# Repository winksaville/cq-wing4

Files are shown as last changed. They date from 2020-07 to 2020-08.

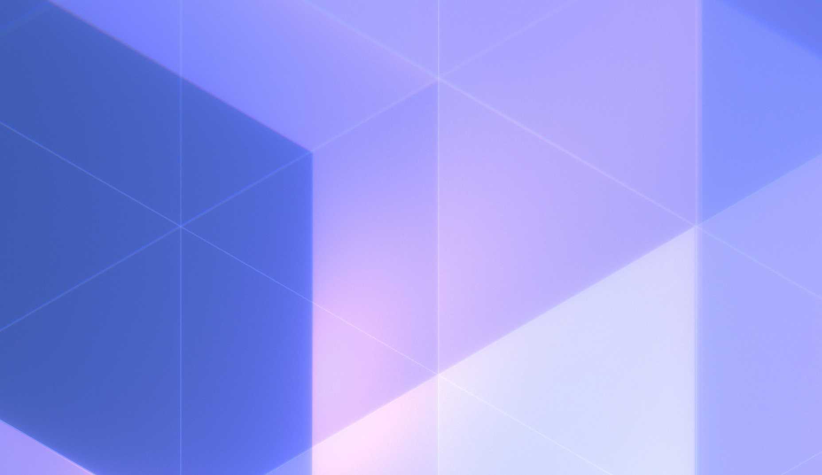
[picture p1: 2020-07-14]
halfWingShell-nrmlTe-shell_+0.1.png

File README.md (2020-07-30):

# Wing with ribs

Wing 4.02

Wing 4.01 had a 8degree kink in the TE so for 4.02 I
flipped the wing over and printed it with LE down instead
of TE down as 4.01 was.

Bad news 4.01 got a kink towards the LE, so that didn't work
and I'll have to change something else, maybe increase diameter
of the cabin.

Another change was to print the dowels with 100% infil up from
50% in 4.01. Because in 4.01 the dowel broke at the wing tail
juncture.

4.02 files pretty well, but took quite a bit LESS ballast on the
nose then I thought it should. I calculated that it should be
about 3.75g but only 1.43g was needed at -60mm.
```
(cq-dev) wink@3900x:~/prgs/CadQuery/projects/wing4 (4.02)
$ ./wing4.02-cg-ballast.py 
noseWeight=7.86g
tailWeight=5.44g
oacWeight=13.3g
oaWeight=13.49g
ballastOffset=-60mm from LE wing
ballast=3.78g
cgLoc=15.00mm from LE wing
cgPct=0.3%
```
It only took 1.43g of ballast
```
(cq-dev) wink@3900x:~/prgs/CadQuery/projects/wing4 (4.02)
$ ./wing4.02-cg.py 
noseWeight=8.15g
tailWeight=6.77g
oacWeight=14.92g
oaWeight=14.91g
ballastOffset=-60 from LE wing
ballast=1.43g
cgLoc=27.12mm from LE wing
cgPct=54.24
```
WHY?

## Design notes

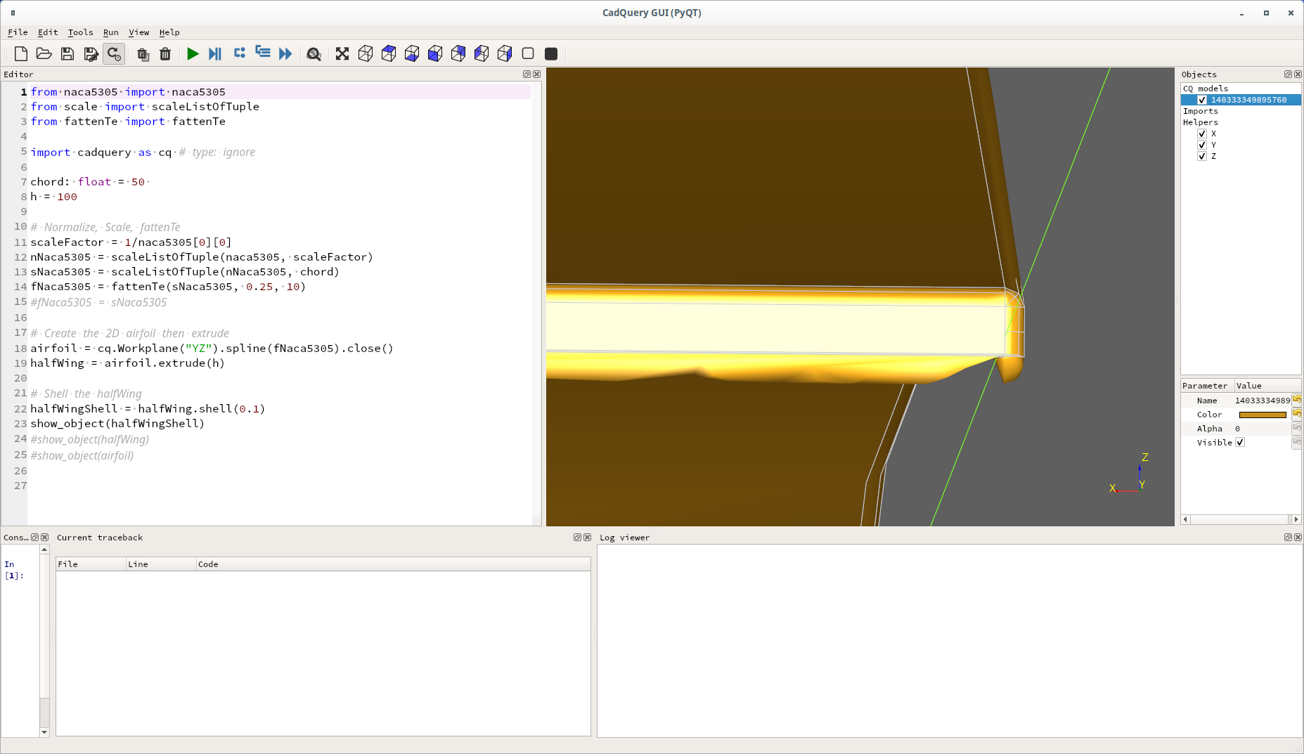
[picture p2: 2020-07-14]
halfWingShell-fatTe-shell_+0.1-yAxis-3.png

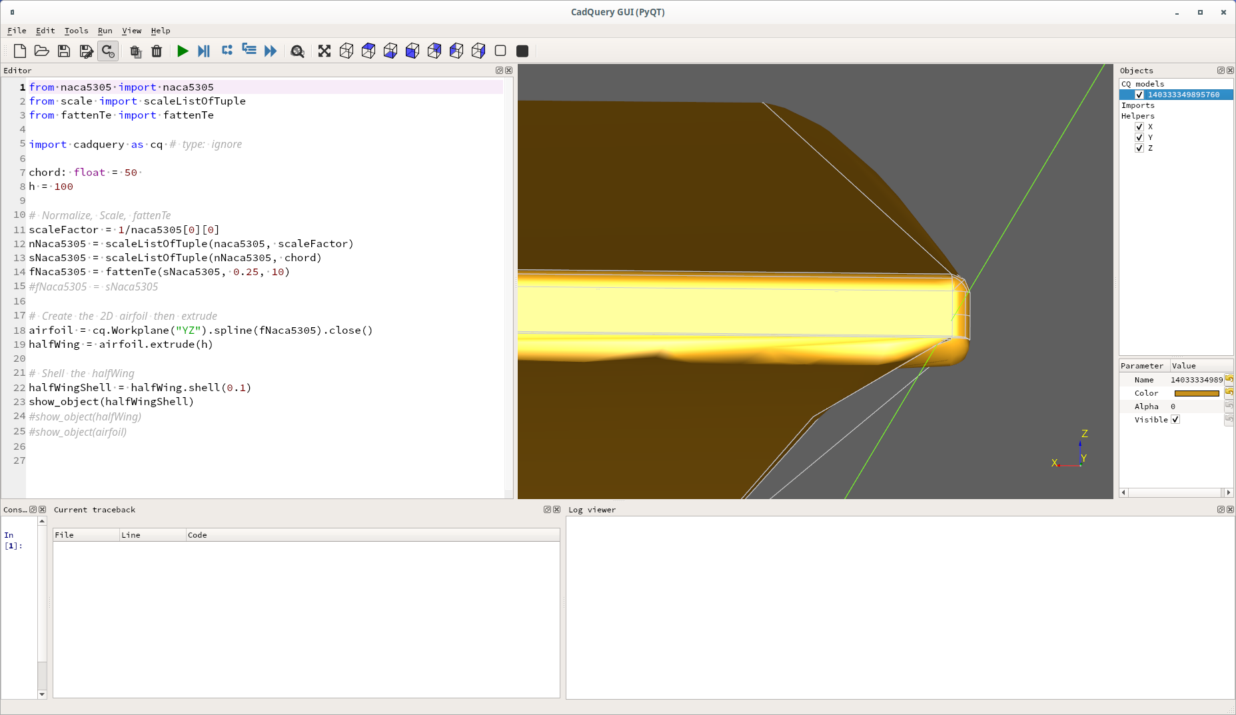
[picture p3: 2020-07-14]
halfWingShell-fatTe-shell_+0.1-yAxis-2.png

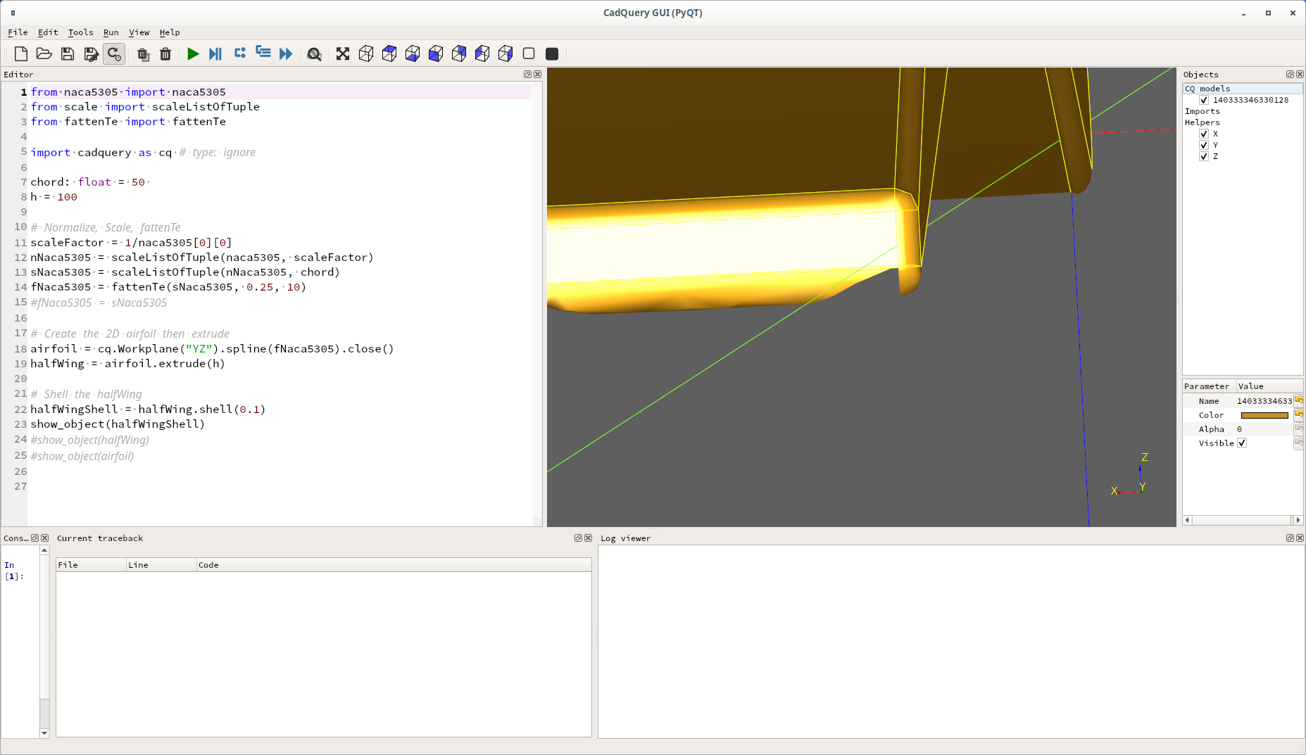
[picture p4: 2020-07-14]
halfWingShell-fatTe-shell_+0.1-yAxis.png

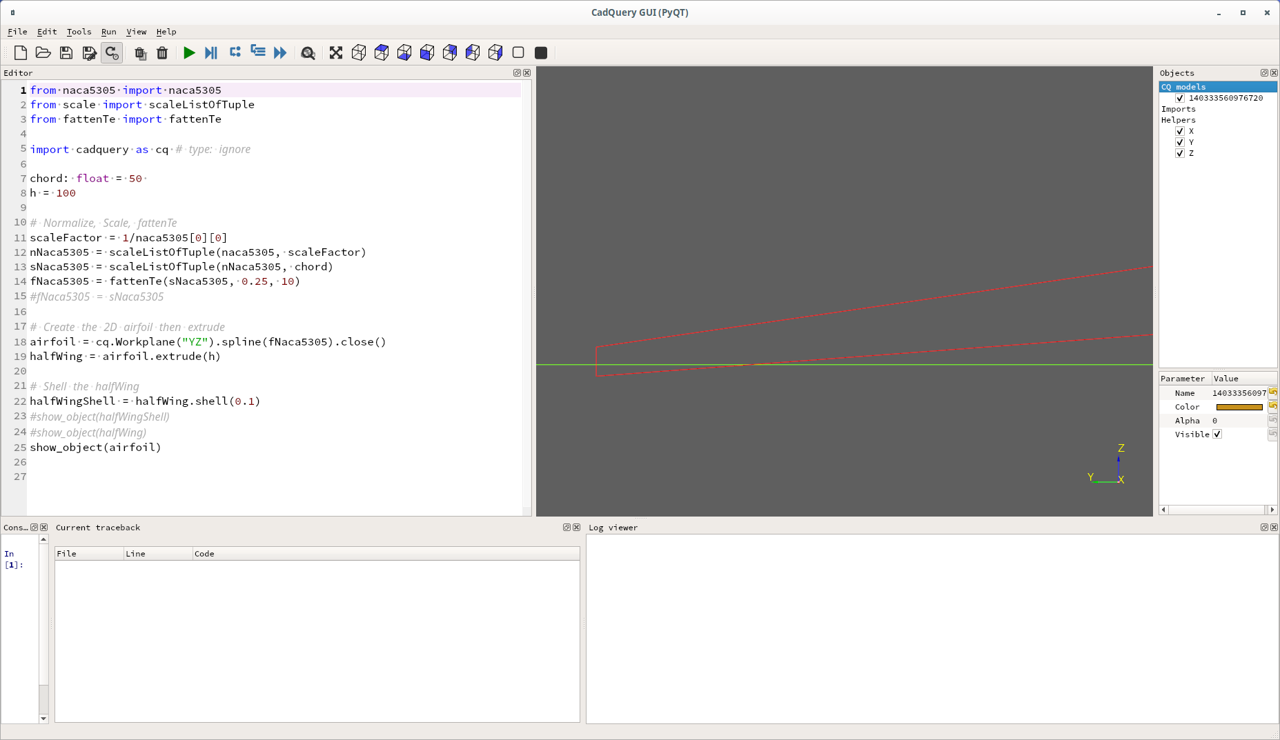
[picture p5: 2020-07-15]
airfoil-fatTe-shell_+0.1.png

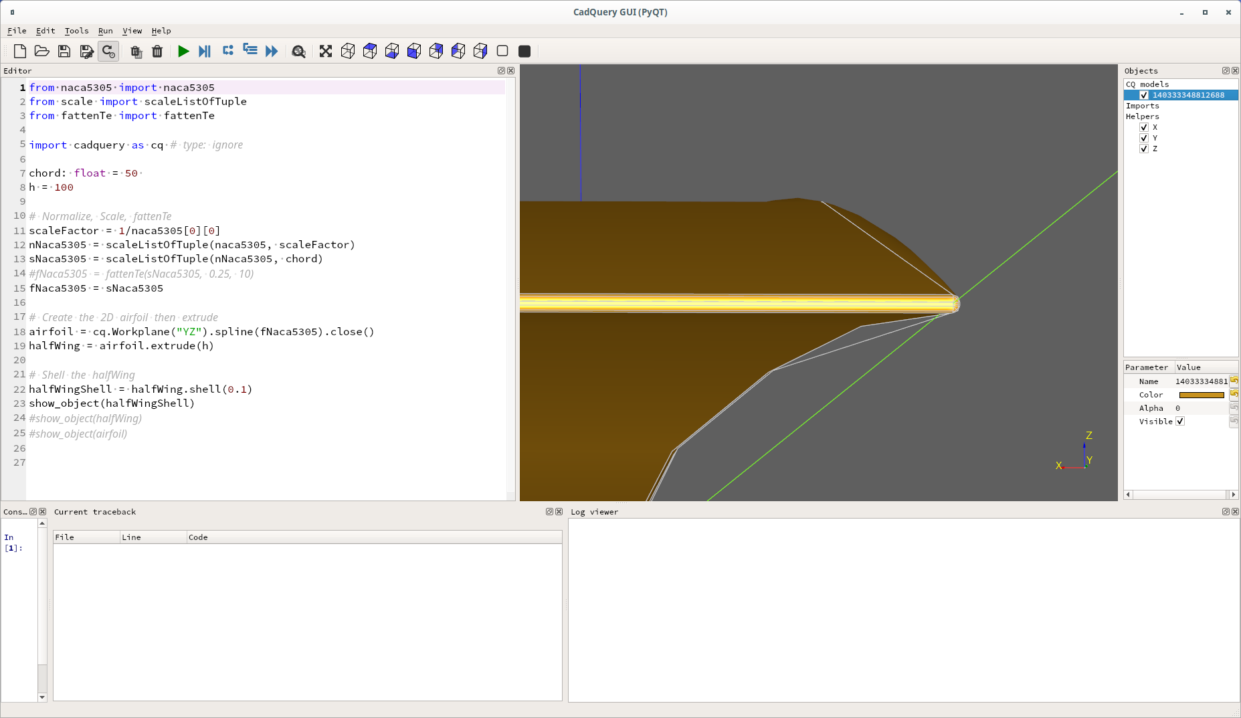
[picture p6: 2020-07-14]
halfWingShell-nrmlTe-shell_+0.1-yAxis-2.png

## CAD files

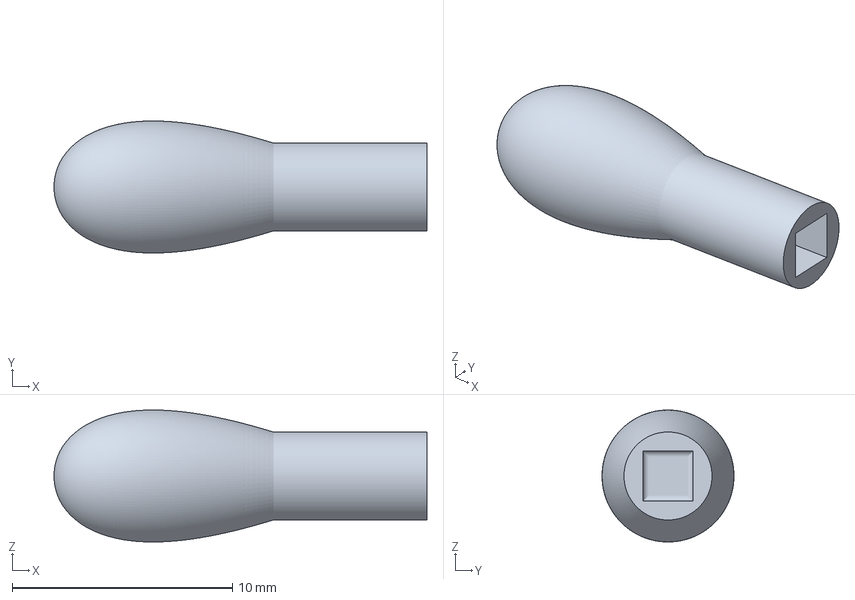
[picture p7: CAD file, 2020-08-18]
ballast-length_22-tol_0.001.3mf
17.0 x 6.00 x 6.00 mm

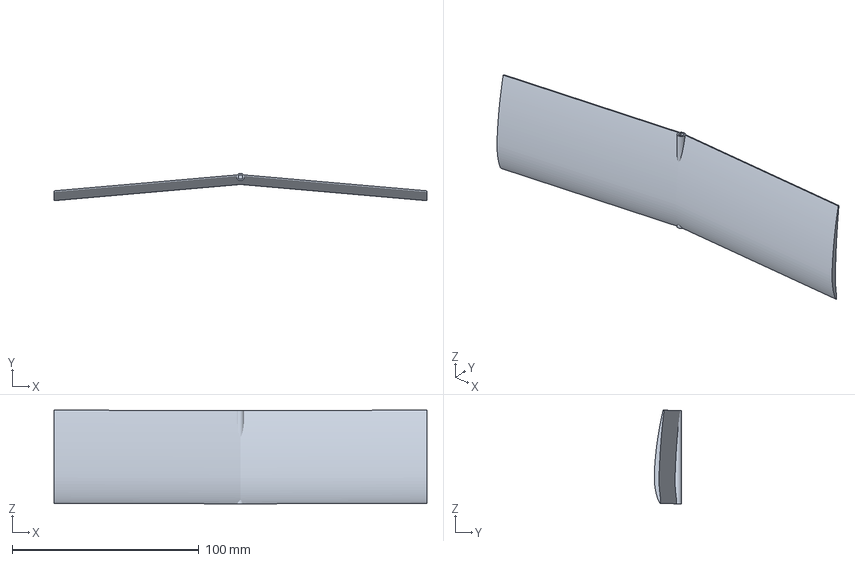
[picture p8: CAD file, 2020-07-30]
wing4.02-LE-down-tol_0.001-ch_50-span_200-di_5-tk_0.26.3mf
200.0 x 14.7 x 50.3 mm

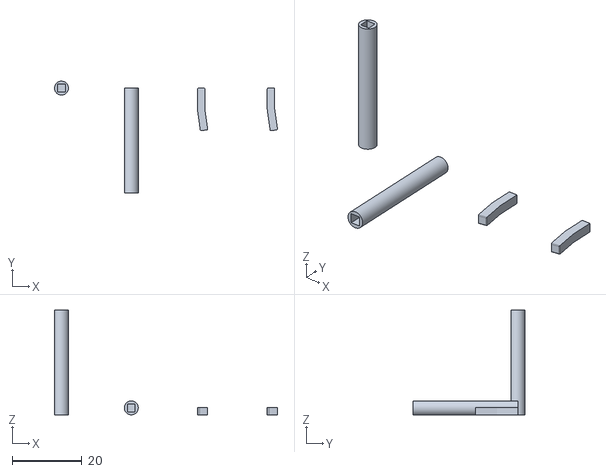
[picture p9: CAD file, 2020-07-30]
rectcon-tol_0.0010-dia_4.0000-x_2.1375-y_2.9402-a_8.0000.stl
63.9 x 32.0 x 30.0

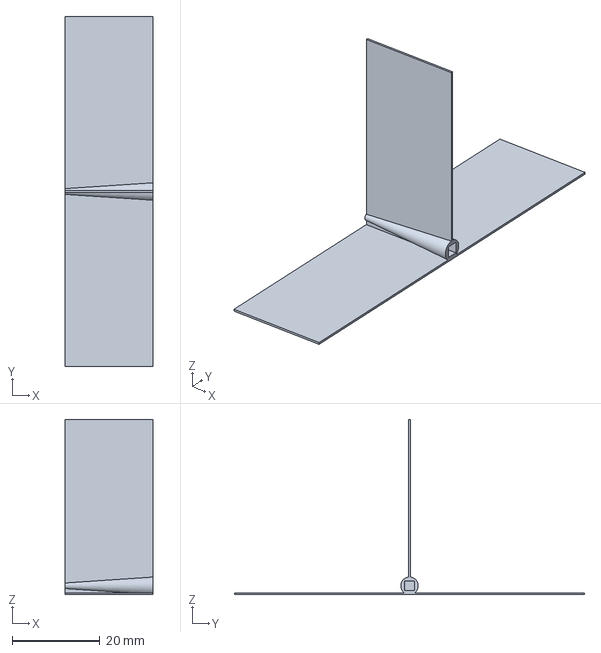
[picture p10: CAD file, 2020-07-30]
tail4-tol_0.001-ch_20-span_80-tk_0.4.3mf
20.0 x 80.0 x 40.0 mm

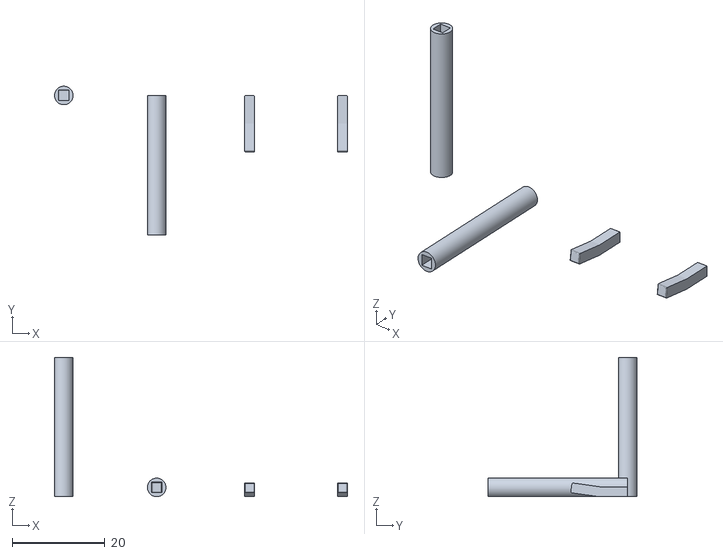
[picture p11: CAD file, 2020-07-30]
rectcon-tol_0.0010-dia_4.0000-x_2.1375-y_2.9402-a_8.0.stl
63.1 x 32.0 x 30.0

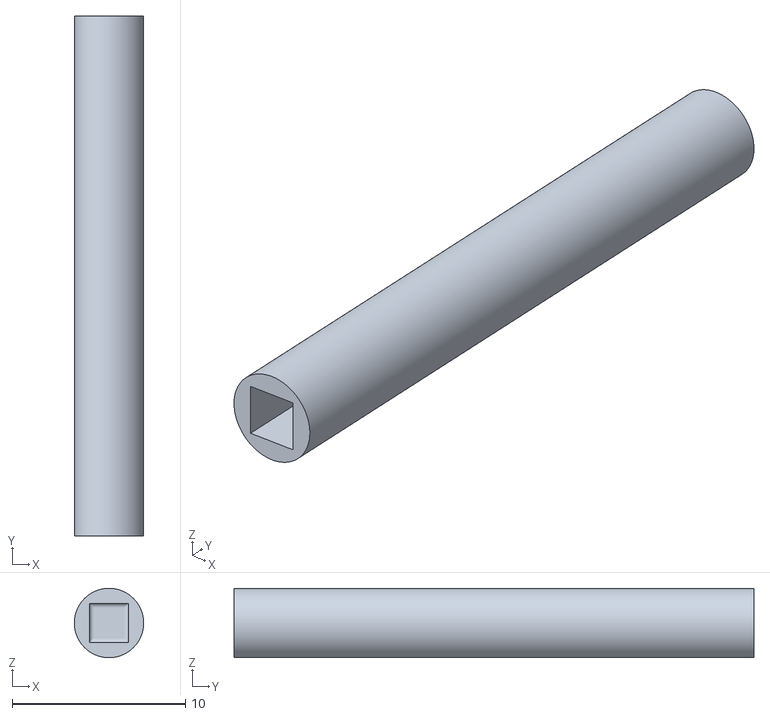
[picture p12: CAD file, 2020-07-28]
beam-tol_0.0010-dia_4.0000-len_30-recv-x_2.2500-y_2.2500-z_6.0000.stl
4.00 x 30.0 x 4.00

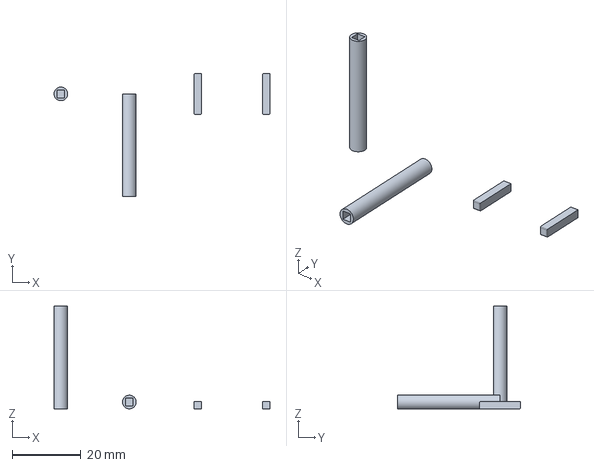
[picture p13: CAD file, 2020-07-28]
rectcon-tol_0.0010-dia_4.0000-x_2.1375-y_2.1375.3mf
63.1 x 36.0 x 30.0 mm

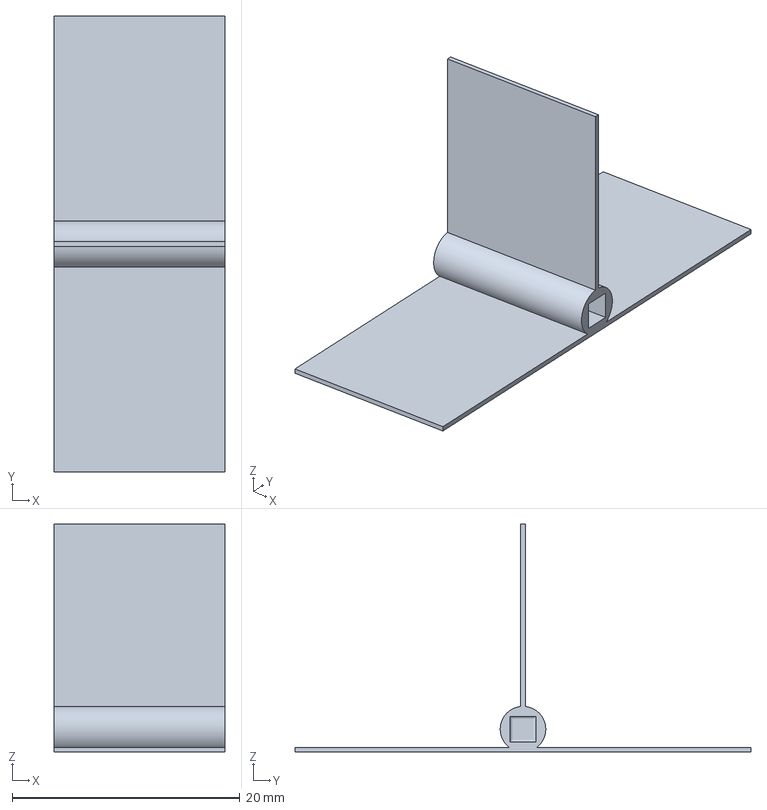
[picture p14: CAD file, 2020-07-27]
tail4-tol_0.001-ch_15-span_40-tk_0.4.3mf
15.0 x 40.0 x 20.0 mm

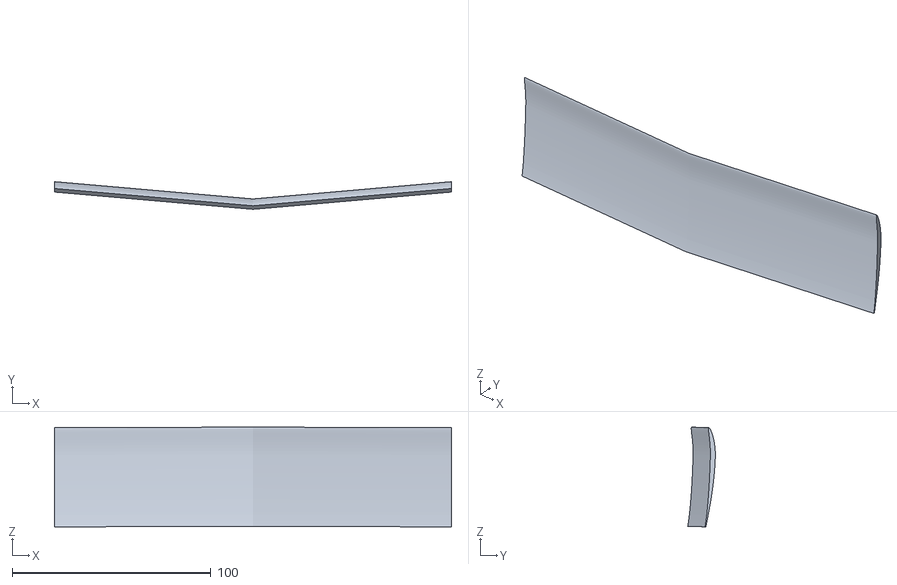
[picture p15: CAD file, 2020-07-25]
wing4-tol_0.001-tk_0.25.stl
200.0 x 14.0 x 50.3

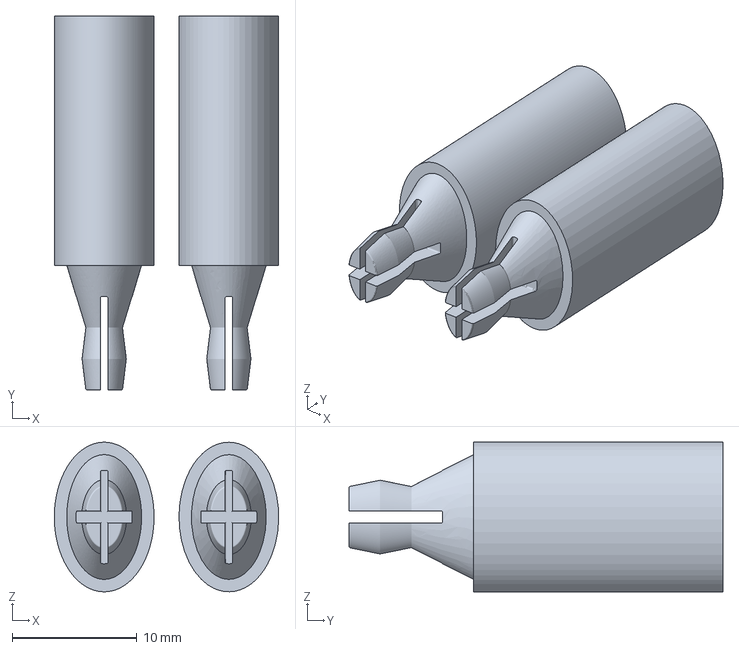
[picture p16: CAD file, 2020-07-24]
elipcon.3mf
18.0 x 30.0 x 12.0 mm

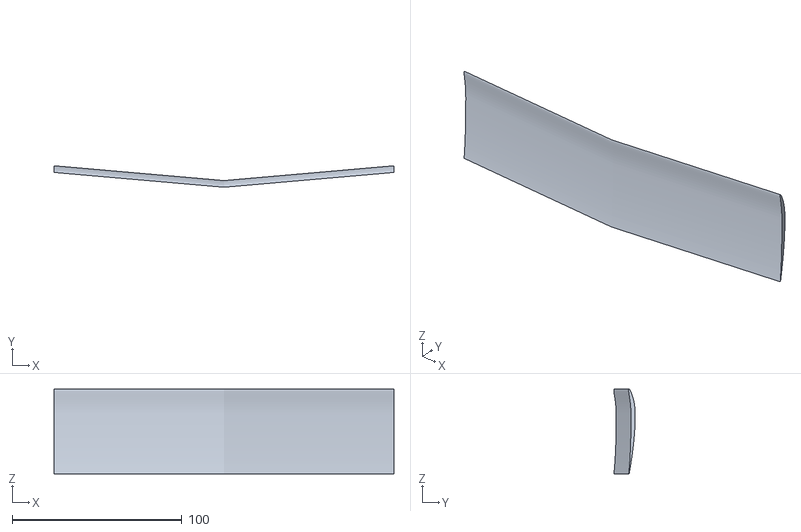
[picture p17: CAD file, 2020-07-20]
wing4-tol_0.001-tk_0.3.stl
200.0 x 12.6 x 50.0

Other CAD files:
rectcon-tol_0.0010-dia_4.0000-x_2.1375-y_2.1375.stl
tail4-tol_0.001-ch_15-span_40-tk_0.4.stl
tail4-tol_0.001-ch_20-span_80-tk_0.4.stl
wing4.02-LE-down-tol_0.001-ch_50-span_200-di_5-tk_0.26.stl

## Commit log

2020-07-14 Initial Commit
    A wing with ribs, not yet working.
    I'm unable to shell a wing created with a spline based airfoil. I get
    the error "Null TopoDS_Shape object":
    (cqgui-master) wink@3900x:~/prgs/CadQuery/projects/wing4 (master)
    $ python nwing.py
    Traceback (most recent call last):
    File "nwing.py", line 30, in <module>
    halfWingShell = halfWing.shell(-0.1)
    File "/opt/anaconda/envs/cqgui-master/lib/python3.7/site-packages/cadquery/cq.py", line 1123, in shell
    s = solidRef.shell(faces, thickness)
    File "/opt/anaconda/envs/cqgui-master/lib/python3.7/site-packages/cadquery/occ_impl/shapes.py", line 1630, in shell
    s1 = self.__class__(shell_builder.Shape()).Shells()[0].wrapped
    File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
    [wing4-direct-0.001.3mf, wing4-direct-0.001.stl]
2020-07-20 Create wing4 with polyline and offset2D
    [wing4-direct-0.001.stl]
2020-07-21 Test wall thickness aka tk of 0.1mm with a 0.25mm nozzle
    With my $5 calipers with a 0.1mm "precision" it actually measured 0.1!
    But the result was unusable, the layers were not sticking well and hence
    the wing was porous and fragile.
    A thickness of 0.30 worked quite well, I wonder how 0.20 and 0.25 might do.
    [wing4-direct-0.001.stl, wing4-tol_0.001-tk_0.1.3mf, wing4-tol_0.001-tk_0.1.stl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]
2020-07-21 Test tk=0.2
    Rename tk_0.1 changed the _PLA to -PLA
    [wing4-tol_0.001-tk_0.2.stl]
2020-07-21 Refactor wing4 into wing and utils
    This "works" either executing directly, `python wing4.py` or
    `cq-editor wing4.py`. One small problem is that I wanted utils.dbg to
    output to the cq-editor log console but that doesn't work so just output
    to terminal for now.
    [wing4-tol_0.001-tk_0.25.stl]
2020-07-22 Refactor scaleAirfoil to airfoil
    - Add airfoil.py and AirfoilSeq and AirfoilList as types
    - Pass airfoilSeq to makeWing
    - Use the airfoil types
    [wing4-tol_0.001-tk_0.25.stl]
2020-07-22 WIP: Elliptical Connector
    Create a elliptical connector which could be round if xLength = yLength
2020-07-24 Update elipcon.py to not use solids()
    This fixes exporting the stl file not having both body1 and body2
    Also separated the body1 and body2 by an additional 10mm.
    [elipcon.3mf]
2020-07-24 Added bodies-sticks
    Actually should probably be called bodies and dowels.
    [bodies-sticks-tol_0.001.3mf, bodies-sticks-tol_0.001.stl, bodies-sticks.stl]
2020-07-24 Add beautifier config files
    This is from:
    https://medium.com/staqu-dev-logs/keeping-python-code-clean-with-pre-commit-hooks-black-flake8-and-isort-cac8b01e0ea1
    [.isort.cfg]
2020-07-25 WIP: Add body to wing
    [wing4-tol_0.001-tk_0.25.stl]
2020-07-27 Lots of stuff
    - fattenTe now smoothly fattens the TE.
    - rectcon is a rectangular connector
    - tail4 is a vtail
    - wing add ribCount, shortCut uses new fattenTe
    - wing4 added a cylindrical cabin
    [bodies-sticks-tol_0.001.3mf, bodies-sticks-tol_0.001.stl, bodies-sticks.stl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]
2020-07-27 Add a dbg print for show_object
2020-07-27 Change tail to flat plates.
    The previous version was a V tail with naca0005 airfoil section but
    it didn't print very well and had to have a 0.40 shellThickness.
    [tail4-tol_0.001-ch_15-span_40-ia_0-di_45-tk_0.26.stl, tail4-tol_0.001-ch_15-span_40-ia_0-di_45-tk_0.3.stl, tail4-tol_0.001-ch_15-span_40-ia_0-di_45-tk_0.4.stl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]
2020-07-28 Change RectCon
    - Changed female and male to receiver and dowel
    - Added dowelHorx
    - Added addReceiver but this is a WIP
    - Added dowellShrinkage precentage and default to 5%
    [rectcon-tol_0.001-rad_2-x_2.25-y_2.25.3mf, rectcon-tol_0.001-rad_2-x_2.25-y_2.25.stl, rectcon-tol_0.001.3mf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]
2020-07-28 Add beam and dowel
    [beam-tol_0.0010-dia_4.0000-len_30-recv-x_2.2500-y_2.2500-z_6.0000.stl, dowel-tol_0.0010-x_2.1375-y_2.1375-z_12.0000.stl]
2020-07-28 gcode fpr tail4, dowels, beams and wing4
    Also 3mf file for wing4, I forgot to save the 3mf file for tail4+.
    [wing4-tol_0.001-ch_50-span_200-di_5-tk_0.26.3mf]
2020-07-30 Angled Dowels
    [dowel-tol_0.0010-x_2.1375-y_2.1375-z_12.0000.stl, dowel-tol_0.0010-x_2.1375-y_2.9402-z_12.2067-a_8.0000.stl, rectcon-tol_0.0010-dia_4.0000-x_2.1375-y_2.9402-a_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]
2020-07-30 Latest tail build
    Remade it after the dowel in the tail broke on a ilttle test flight.
    [tail4-tol_0.001-ch_20-span_80-tk_0.4.3mf]
2020-07-30 Rotate dowels so angled dowels will be on their side
    [rectcon-tol_0.0010-dia_4.0000-x_2.1375-y_2.9402-a_8.0000.stl]
2020-07-30 dowels 50% infil
    Still not strong enough, on second flight broke off at base of main wing.
    [dowel-5_0deg-3_8deg-IF_50pct-tol_0.0010-x_2.1375-y_2.1375-z_12.0000.3mf]
2020-07-30 Calculate GC and Ballast for Wing4 01
2020-07-30 Wing 4.02
    Flies and the dowels at 100% infill haven't broken! But the horizontal
    stabilizer TE has delaminated, and the wing has kinked. So flipping the
    wing so it prints with LE down didn't help.
    Ballast wise it took less weight then I thought it should, no idea why?
    [dowel-7_0deg-3-8deg-IF_100pct-tol_0.0010-x_2.1375-y_2.1375-z_12.0000.3mf, dowel-tol_0.0010-x_2.1375-y_2.1375-z_12.0000-a_0.0000.stl, dowel-tol_0.0010-x_2.1375-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]
2020-08-06 Add command line parameters
    Added -a --angle, -lp --linearPrecision, -ap --angularPrecision.
    [dowel-5_0deg-3_8deg-IF_50pct-tol_0.0010-x_2.1375-y_2.1375-z_12.0000.3mf, dowel-7_0deg-3-8deg-IF_100pct-tol_0.0010-x_2.1375-y_2.1375-z_12.0000.3mf, dowel-lp_0.0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]
2020-08-06 Add more arguments to dowel
    rectcon.py
    - change dowelShrinkage to dowelClearene in RectCon.
    - add dowel_zLen
    [dowel-lp_0.0010-ap_1-x_2.1500-y_2.1500-z_5.9000-a_0.0000.stl, dowel-lp_0.0010-ap_1.0-x_2.1375-y_2.1375-z_12.0000-a_0.0000.stl, dowel-lp_0.0010-ap_1.0-x_2.1375-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]
2020-08-08 Update dowel to ise angularTolerance
    They accepted my change but Adam decided to change the convention he
    introduced from angularPrecision to angularTolerance.
    [dowel-lp_0.0010-ap_1-x_2.1500-y_2.1500-z_5.9000-a_0.0000.stl]
2020-08-10 Rename utils.py to wing_utils.py
    I'm doing this because at times mypy seems to get confused with utils.py
    in cadquery. Could be mistaken, but this won't hurt.
2020-08-15 Get split_2d working enough for airfoils
    - Added supporting method in wing_utils.py
    - Add some tests, but more are needed
    - Add t target for testing in Makefile
2020-08-16 Executing make f succeeds on all files
    The version of mypy is master from last week
    (cq-dev) wink@3900x:~/prgs/CadQuery/projects/wing4 (master)
    $ mypy --version
    mypy 0.790+dev.0dfac58ede61f7c4a92f55ffe5f527fa6781fab2.dirty
2020-08-17 Add ballast.py
    Noesn't pass mypy yet, but is "working" but not complete need to
    add female connector to beam and then union beam and bulb at a minimum.
2020-08-18 Output stl
    And increase length of stub so more material between end of rectcon and
    the interior of ballast bulb.
    TODO: ballast bulb needs to be bigger probably 20 or 25mm in length.
    [ballast-length_22-tol_0.001.3mf]
2021-03-24 Add dist_2d and dist_3d to wing_utils.py
